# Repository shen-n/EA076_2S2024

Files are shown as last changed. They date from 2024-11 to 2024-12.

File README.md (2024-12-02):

# `ObservaCÃO - um ajudante para observação do céu noturno` ([Manual de Uso aqui](https://github.com/shen-n/EA076_2S2024/blob/main/manual_de_uso.md))

Este trabalho trata-se do projeto final da disciplina *EA076 (Laboratório de Sistemas Embarcados)*, ministrada pelo Prof. Dr. Fabiano Fruett no segundo semestre de 2024. Ele foi baseado no trabalho "[_Star Track - Arduino Powered Star Pointer and Tracker_](https://www.instructables.com/Star-Track-Arduino-Powered-Star-Pointer-and-Tracke/)", de Görkem, sendo adaptado para operar com a placa BitDogLab.

|Nome do aluno  | RA | Curso|
|--|--|--|
| Felipe Hiroshi Kano Inazumi | 215696  | Eng. Elétrica|
| Nathan Shen Baldon  | 242448 | Eng. Elétrica|

## Descrição do Projeto

O projeto buscou a construção de um sistema capaz de apontar para corpos celestes com um laser, independente da posição do observador. Para isso, deve-se fornecer ao dispositivo as coordenadas do corpo celeste que se deseja observar. Um dos requisitos foi de que o dispositivo construído fosse _wireless_, ou seja, independente de cabos para alimentação e comunicação, para que pudesse ser usado em campo com maior facilidade. 

Potenciais usuários:
- amantes de astronomia e astrofotografia;
- educadores;

## Metodologia

O desenvolvimento deste projeto envolveu quatro frentes: (a) estudo teórico sobre localização de corpos celestes (resumido no sistemas de coordenadas escolhido); (b) escolha de materiais; (c) desenvolvimento e fabricação de uma estrutura mecânica; (d) desenvolvimento e fabricação de uma PCB; (e) desenvolvimento do programa. 

### Sistemas de coordenadas

Optou-se por utilizar coordenadas do Sistema Horizontal neste projeto, ou seja, são usados os valores de Azimute e Altitude para localização de cada corpo celeste. O seguinte _site_ foi usado para determinação das coordenadas: [base de dados de corpos celestes](https://www.timeanddate.com/astronomy/night/). Mais detalhes sobre sistemas de coordenadas são fornecidos no **Apêndice A**.

### Materiais Utilizados

Os materiais escolhidos e utilizados são descritos na tabela a seguir. Se desejado, pode-se clicar no nome do material para ser redirecionado para o site de um fornecedor.

|Materiais | Qtde. | Descrição |
|--|--|--|
| [Placa BitDogLab](https://github.com/BitDogLab/BitDogLab/tree/main) | 1 | Controle do projeto. Além disso, os botões e joystick da placa também foram utilizados para controle pelo usuário. |
| [Motor de Passo 17HS4023](https://pt.aliexpress.com/item/1005007232266402.html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) | 2 | Para movimentar o laser. |
| [Driver DRV8825](https://pt.aliexpress.com/item/4000083334758.html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) | 2 | Para realizar a interface entre BitDogLab e motores. Este driver utiliza a interface STEP/DIR, que facilita o controle dos motores, sendo necessários apenas 2 pinos na BitDogLab (mais detalhes no **Apêndice B**). |
| [Bateria 3S](https://pt.aliexpress.com/item/1005003835491136.html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) | 1 | Para que o ObservaCÃO seja independente da rede elétrica. |
| [Laser](https://pt.aliexpress.com/item/1005006719063413.html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) | 1 | Para apontar para os corpos celestes. |
| [Módulo Bluetooth HC-05](https://www.eletrogate.com/modulo-bluetooth-rs232-hc-05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[MC4]_[G]_[PMax]_Categorias&utm_content=&utm_term=&gad_source=1&gclid=CjwKCAiAjKu6BhAMEiwAx4UsAqtbrS_S_TdBN0OxV5r_2TgRlhCnLvffXhJ7JxJXbR2puQFTbAGGFxoC9gUQAvD_BwE) | 1 | Para que as coordenadas dos corpos celestes fossem passadas para a BitDogLab sem necessidade de fios. |
| [Parafusos M3 10 mm](https://pt.aliexpress.com/item/1005007219475077.html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) | 4 | Para montagem de um dos motores de passo na estrutura mecânica. |
| [Conector XT30pw fêmea 90 graus](https://pt.aliexpress.com/item/1005004957495676.html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) | 1 | Para conexão da bateria na PCB criada. |
| [Cabo com conector JST 4 pinos](https://www.makerhero.com/produto/conector-jst-4-pinos-femea/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) | 4 | Para conexão entre a BitDogLab e a PCB desenvolvida. |
| [Conector JST 4 pinos macho (I2C)](https://www.makerhero.com/produto/conector-jst-4-pinos-macho/) | 3 | Utilizados na PCB criada para conexão com a BitDogLab. |
| [Conector IDC Box 14 pinos macho](https://pt.aliexpress.com/item/1005006804603387.html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) | 1 | Utilizado na PCB criada para conexão com a BitDogLab. |
| [Cabo flat com conector IDC Box 14 pinos](https://pt.aliexpress.com/item/1005003161799870.html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) | 1 | Para conexão entre a BitDogLab e a PCB desenvolvida. |

### Estrutura Mecânica

Para integrar os motores e o laser, foi desenvolvida uma estrutura mecânica, composta de quatro partes. Elas foram desenvolvidas no _software_ AutoCad Inventor e estão na pasta [3d_models](https://github.com/shen-n/EA076_2S2024/tree/main/3d_models). As peças foram fabricadas em uma impressora 3D, utilizando filamento PLA na cor branca. A montagem foi feita conforme o arquivo [assembly.stl](https://github.com/shen-n/EA076_2S2024/blob/main/3d_models/assembly.stl). O motor da base é utilizado para determinar a coordenada Azimute e, o motor superior, para a coordenada Altitude. Assim, ao longo da documentação, são muitas vezes chamados de motores de passo Azimute e Altitude. 

### Desenvolvimento da PCB

O desenvolvimento da PCB foi feito com o auxílio do software KiCad 8.0, os arquivos de fabricação, esquemático e layout estão compactados e podem ser encontrados na pasta [PCB](https://github.com/shen-n/EA076_2S2024/tree/main/PCB).

O esquemático da placa contém um conector Box IDC de 14 pinos, necessários para realizar a comunicação das GPIOs da BitDogLab com os drives DRV8825 na PCB. Além disso, a placa possui 1 conector de dois terminais para fazer a ligação do laser e do lado destes conectores estão dispostos dois conectores I2C nos quais devem ser conectados os motores de passo superior e inferior. Para mais detalhes da PCB e o esquema de ligação veja o capítulo [Descrição Estrutural](#Descrição-Estrutural)

O circuito para acionamento do Laser foi desenvolvido com um chaveamento simples controlado por transistor conforme apresentado na figura abaixo. Para controlar o chaveamento deste transistor é necessário fazer a conexão do IDC0 no conector J7 da placa.

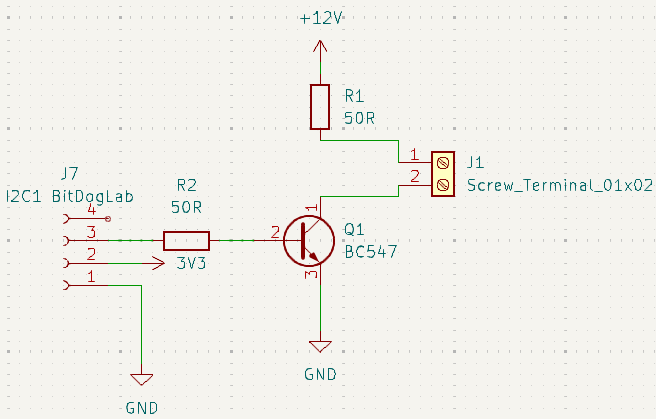
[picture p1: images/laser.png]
Laser


Além disso, a placa também conta com um header J9 de 6 pinos que permite acesso aos GPIOS 08 e 09 além do VCC e GND. 

A alimentação da placa deve ser conectada com uma bateria 3S (11.1 V) via conector XT30. Contudo, a placa também pode ser alimentada com uma tensão de até 12V, que seria a tensão nominal do motor de passo escolhido no projeto.

### Desenvolvimento do programa 

O programa utilizado neste projeto foi desenvolvido na linguagem de programação micropython e utiliza as seguintes bibliotecas:
- Machine
- Time
- Sys
- Ssd1306
- Framebuf
  
A comunicação com o módulo bluethooh foi feita via protocolo UART, e mais especificamente foi utilizada a UART0 da Raspiberry neste projeto. 

O programa inicia com uma função de calibração controlada via Joystick da BitDogLab, de tal forma que, o usuário deverá utilizar movimentos do joystick para cima/baixo ou para a esquerda/direita para controlar os motores superiores e inferiores de tal forma a alinhar o laser na posição horizontal e na direção do polo norte.

Cada comando direcional do Joystick envia o comando de 1 passo para o respectivo motor (superior ou inferior). Quando o usuário pressiona o botão central do Joystick, um delay é adicionado entre cada comando de 1 passo para o motor, resultando em um movimento mais sensível e permitindo assim uma calibração fina dos motores. Esse pressionar do botão do Joystick alterna entre os modos de calibração fina e mais rápida. Para confirmar a calibração estabelecida, o usuário deve pressionar o botão B para avançar para a próxima etapa do programa. Neste momento, o programa entende que a posição atual dos motores é a referência (0,0).

Em seguida, o programa aguarda o envio das coordenadas, via módulo bluetooth, do astro a ser apontado. As coordenadas devem ser enviadas no formato:

````
Azimuth,Altitude 
````

Note que estas coordenadas podem ser do tipo float com precisão de 2 casas decimais, e não deve haver espaço entre a virgula. Ambos as coordenadas podem ser valores negativos e caso o valor azimutal seja maior que 180°, o programa converte este valor de ângulo positivo para o respectivo ângulo negativo para evitar que o motor inferior rotacione mais do que o necessário.

Por fim, o programa calcula o número de micropassos necessários para cada motor de tal forma que, o motor finalize o movimento no ângulo enviado pelo usuário.

Alguns exemplos de comandos enviados na sequência:

Enviando 45,45
````
45,45
````
O motor inferior irá girar 45° para Leste e o motor superior irá rotacionar 45° para cima, resultando em Azimuth: 45°, Altitude: 45°

Enviando 90,90
````
90,90
````
O motor inferior irá girar 45° novamente para Leste e o motor superior irá rotacionar novamente 45° para cima, resultando em Azimuth: 90°, Altitude: 90°

Enviando 0,0
````
0,0
````
O motor inferior irá girar -90° para Leste (equivalente à 90° para oeste) e o motor superior irá rotacionar -90° para cima (equivalente à 90° para baixo), resultando em Azimuth: 0°, Altitude: 0° (origem)

Enviando 270,0
````
270,0
````
O motor inferior irá girar 270° para Leste (equivalente à 360-270 = 90° para oeste) e o motor superior irá rotacionar 0° para cima resultando em Azimuth: -90°, Altitude: 0° 

Entre cada envio das coordenadas, o usuário também pode pressionar o Botão A ou Botão B da BitDogLab e uma das situações a seguir deve ocorrer:
- Botão A: Alterna o estado do Laser para Ligado/Desligado
- Botão B: O programa entra no modo de calibração, conforme mencionado anteriormente, sendo necessário pressionar novamente o botão B para concluir a calibração. 

Abaixo é apresentado um fluxograma do programa descrito

- **Fluxograma:**



## Descrição Estrutural

Para que se compreenda a conexão entre os diferentes componentes, foi criada a tabela abaixo, que apresenta qual GPIO da BitDogLab foi atribuída a cada pino de cada periférico. Além disso, na coluna mais à direita, é apresentado em qual conector cada GPIO se situa.

Obs: note que os pinos de ajuste de micropasso dos dois _drivers_ (M0, M1 e M2) estão conectados entre si, não sendo possível configurá-los de forma independente.

### Conexões com BitDogLab
<table><thead><tr><th></th><th>Pino</th><th>GPIO</th><th>Conector BitDogLab</th></tr></thead><tbody><tr><td rowspan="5">Driver 1 (motor Altitude)</td><td>M0</td><td>19</td><td rowspan="10">IDC box 14 pinos</td></tr><tr><td>M1</td><td>20</td></tr><tr><td>M2</td><td>18</td></tr><tr><td>DIR</td><td>4</td></tr><tr><td>STEP</td><td>28</td></tr><tr><td rowspan="5">Driver 2 (motor Azimute)</td><td>M0</td><td>19</td></tr><tr><td>M1</td><td>20</td></tr><tr><td>M2</td><td>18</td></tr><tr><td>DIR</td><td>17</td></tr><tr><td>STEP</td><td>16</td></tr><tr><td>Laser</td><td>-</td><td>2 (SDL)</td><td>I2C1</td></tr><tr><td rowspan="4">Módulo Bluetooth HC-05</td><td>RX</td><td>0 (SDA)</td><td rowspan="4">I2C0</td></tr><tr><td>TX</td><td>1 (SCL)</td></tr><tr><td>VCC</td><td>3V3</td></tr><tr><td>GND</td><td>GND</td></tr></tbody></table>

Também, para facilitar a montagem, a figura abaixo mostra quais conexões devem ser feitas entre a BitDogLab e todos os periféricos.

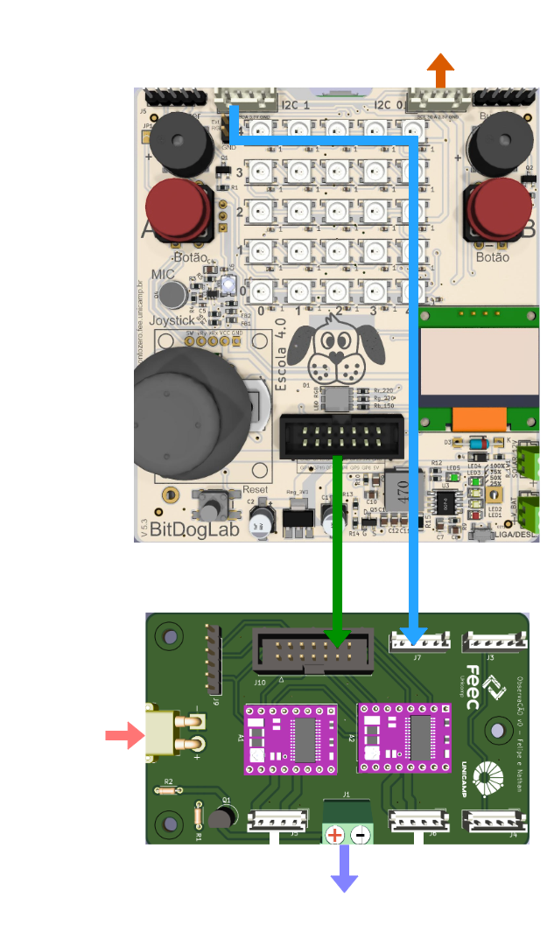
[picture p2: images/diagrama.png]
diagrama


## Resultados

A figura abaixo apresenta o resultado da montagem da estrutura mecânica. Como pode se constatar, ficou exatamente conforme o modelo 3D projetado.

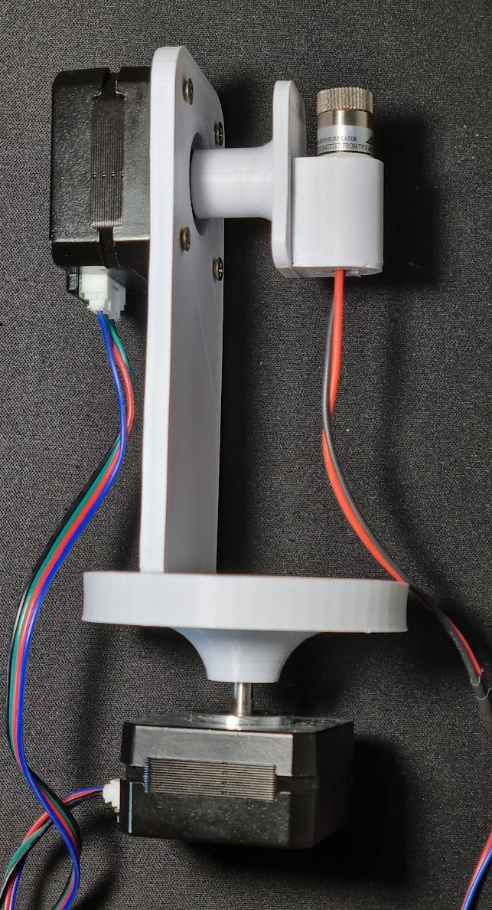
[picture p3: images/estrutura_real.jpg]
estrutura_real


A montagem da PCB também foi um sucesso, sendo apresentada abaixo.

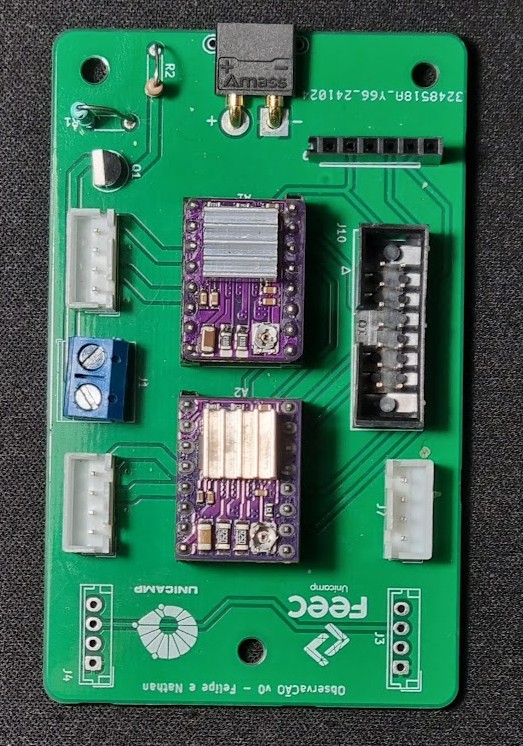
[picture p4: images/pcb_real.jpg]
pcb_real


Em relação ao funcionamento do dispositivo para observação do céu, não foi possível visualizar o _laser_ durante a noite (muito fraco), sendo que não foi possível analisar sua precisão. No entanto, foram utilizados aplicativos de celular que localizam corpos celestes (e.g. [Star Walk 2](https://play.google.com/store/apps/details?id=com.vitotechnology.StarWalk2Free&hl=pt_BR)) e, em testes, o sistema ObservaCÃO apontou aproximadamente para a mesma direção indicada pelos aplicativos, mostrando potencial. No entanto, havia sempre algum erro entre o celular e o dispositivo, principalmente pela calibração falha em **ambos** os dispositivos, o que será discutido na próxima seção.  

## Desafios e Conclusão

Ao longo do desenvolvimento do projeto, houve apenas desafios pequenos. Primeiramente, pode-se citar o mau funcionamento das GPIOs 8 e 9 (UART1), que seriam usadas com o módulo bluetooth HC-05. Em nenhum momento, foi possível ler ou escrever dados com estes pinos, mesmo realizando a atribuição explícita deles para UART1 no programa. Assim, foi necessário utilizar a UART0 (GPIOs 0 e 1), a qual funcionou. No tempo do projeto, não foi possível identificar o problema com a UART1. Vale comentar também que o módulo bluetooth apresentou inconsistências, ora lendo e escrevendo corretamente, ora não.

Outro problema encontrado ao longo do desenvolvimento do projeto foram falhas em fios/cabos: um deles foi um _jumper_ de _protoboard_, o qual estava rompido internamente; outro foi com a crimpagem do cabo flat utilizado, que apresentou falhas de continuidade e precisou ser ajustado.

Por fim, o desafio mais relevante foi aquele relacionado com erros na indicação de corpos celestes. Uma das grandes fontes de erro foi a calibração do celular, que estava sendo usado como referência de bússola e como referência da localização dos corpos celestes. Note que, neste caso, qualquer erro nesta referência causa erros no dispositivo ObservaCÃO e a própria indicação dos astros dada pelo celular pode estar também equivocada. Para corrigir isso, poderia ter sido utilizado o Sistema Equatorial (descrito no **Apêndice A**) e alguma estrela conhecida como referência, o que eliminaria, ao menos, uma fonte de erro. A dificuldade de se usar este sistema, entretanto, foi de que toda a estrutura mecânica teria de ser alinhada com o plano fundamental desse sistema, o que não foi possível neste projeto, mas que poderia ser considerado em uma próxima versão do dispositivo.

Assim, encerra-se indicando possíveis melhorias futuras: (a) melhorar estabilidade da estrutura mecânica, a qual atualmente tomba durante movimentos bruscos dos motores; (b) adicionar peça para acoplamento do dispositivo ObservaCÃO com tripé, o que permitiria incliná-lo e alinhá-lo com o plano fundamental do Sistema Equatorial; (c) adicionar conexão entre pinos ENABLE dos drivers e BitDogLab, para que seja possível ativar e desativar os motores quando desejado, o que aumentaria a autonomia da bateria.

## Referências

[1] GörkemPortfolio, “Star Track - Arduino Powered Star Pointer and Tracker,” Instructables. https://www.instructables.com/Star-Track-Arduino-Powered-Star-Pointer-and-Tracke/

[2] “Coordinate Systems Comparison,” Unl.edu, 2024. https://astro.unl.edu/classaction/animations/coordsmotion/celhorcomp.html.

[3] “Galileo’s Finger - an Open Source Astronomy Learning Tool,” Instructables, Mar. 30, 2015. https://www.instructables.com/Galileos-Finger-An-Open-Source-Astronomy-Learning-/.

[4] P. Dyches, “What is the North Star and How Do You Find It? - NASA Science,” science.nasa.gov, Jul. 28, 2021. https://science.nasa.gov/solar-system/skywatching/what-is-the-north-star-and-how-do-you-find-it/

[5] “The North Star: Polaris,” Space.com, May 16, 2017. https://www.space.com/15567-north-star-polaris.html

[6] “Horizontal and equatorial coordinate systems,” Astronomy Stack Exchange, Dec. 31, 2021. https://astronomy.stackexchange.com/questions/48004/horizontal-.

[7] “Sistema horizontal de coordenadas,” Wikipedia.org, Jul. 2007. https://pt.wikipedia.org/wiki/Sistema_horizontal_de_coordenadas.

[8] “The Internet Stellar Database,”. http://www.stellar-database.com/

## Apêndice A - sistemas de coordenadas

Para localizar corpos celestes, é muito comum que se utilize o sistema de coordenadas celeste. Nele, usa-se o conceito de Esfera Celeste: uma projeção de todo o céu em uma esfera de raio indeterminado e concêntrica à Terra (como se o céu que vemos fosse uma casca esférica ao redor da Terra). A localização dos corpos se dá através de coordenadas esféricas, as quais dependem do plano fundamental escolhido (plano que divide Esfera Celeste em dois hemisférios) [1]. O Sistema Horizontal, por exemplo, é geralmente mais conhecido (com Azimute/Altitude como coordenadas) e utiliza o horizonte local do observador como plano fundamental [1,7]. O problema é que, como a referência (plano fundamental) depende da posição do observador na Terra, a posição do corpo celeste a ser apontado, por consequência, também depende. Assim, para eliminar essa dependência, é comum que se utilize o Sistema Equatorial, que toma como plano fundamental o Equador Celeste (projeção da Linha do Equador na Esfera Celeste) [1,6]. O Polo Norte e Polo Sul também são projetados na Esfera Celeste, sendo denominados Polo Sul Celeste e Polo Norte Celeste.

As coordenadas são dadas em Ascenção Reta e Declinação:
- Declinação (DEC): ângulo entre Equador Celeste e Polos Norte ou Sul Celestes (varia de -90 a 90°).
- Ascensão Reta (RA): ângulo ao longo do Equador Celeste em relação a uma referência zero (ponto vernal - equivalente ao Meridiano de Greenwich como referência de longitude). Ele é dado em horas, minutos e segundos, de forma que uma volta completa equivale a 24h.

Assim, para localizar os corpos celestes, pode-se utilizar uma base de dados que indique as coordenadas no Sistema Equatorial [1,8]. Também, o sistema precisa saber onde estão as referências de posição necessárias:
- Referência para DEC: uma alternativa é encontrar o Polo Norte Celeste, que pode ser encontrado através da Estrela Polar (Polaris) [1,4,5]. Assim, seria necessário apontar para esta Estrela manualmente, indicando para o sistema sua posição (obs: esta estrela é visível apenas no hemisfério Norte, sendo necessário outra referência para observadores do hemisfério Sul).
- Referência para RA: pode-se utilizar o tempo sideral, que também tem como referência o ponto vernal (referência de RA). O tempo sideral pode ser calculado a partir do horário local. [1]

## Apêndice B - driver DRV8825

O driver DRV8825 possui duas pontes H e é projetado para controle de motores de passo bipolares. O controle é feito com a interface STEP/DIR, entradas que indicam quantos passos devem ser dados (definido pelo número de pulsos em STEP) e em qual direção (definido pelo nível lógico em DIR) (figura abaixo). 

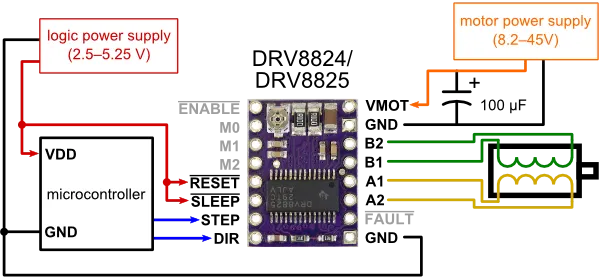
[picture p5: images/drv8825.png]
drv8825

Retirado de: [fonte](https://www.marinostore.com/automacao/driver-motor-de-passo-drv8825)

Para controle do tamanho do passo (microstep), é necessário introduzir uma combinação de valores binários nas entradas M0, M1 e M2, conforme apresentado na tabela abaixo. O driver possui uma resistência de pulldown interna, de tal forma que, se a entrada estiver desconectada o nível de tensão neste terminal está em 0V (GND).

<table><thead><tr><th>M2</th><th>M1</th><th>M0</th><th>Tamanho do Passo</th></tr></thead><tbody><tr><td>0</td><td>0</td><td>0</td><td>Passo completo</td></tr><tr><td>0</td><td>0</td><td>1</td><td>1/2 Passo</td></tr><tr><td>0</td><td>1</td><td>0</td><td>1/4 Passo</td></tr><tr><td>0</td><td>1</td><td>1</td><td>1/8 Passo</td></tr><tr><td>1</td><td>0</td><td>0</td><td>1/16 Passo</td></tr><tr><td>1</td><td>0</td><td>1</td><td rowspan="3"><br><br>1/32 Passo</td></tr><tr><td>1</td><td>1</td><td>0</td></tr><tr><td>1</td><td>1</td><td>1</td></tr></tbody></table>

Outra etapa necessária para o funcionamento do driver DRV8825 é a calibração da corrente de saída do driver. Esta calibração é feita alterando a posição do potenciômetro disponível no próprio driver, e fazendo a medição do valor de tensão entre este ponto e o GND. 

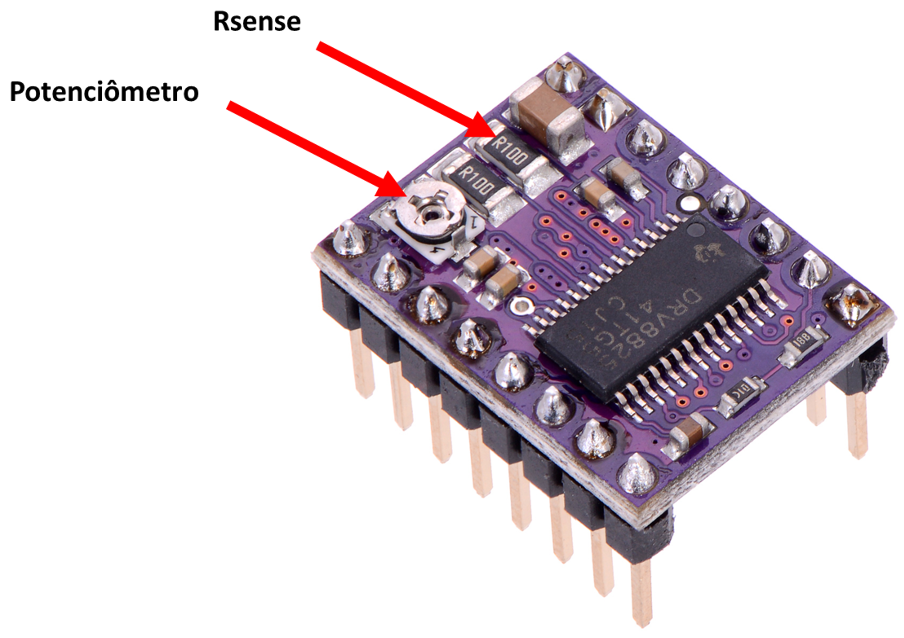
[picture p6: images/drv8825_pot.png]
drv8825_pot


Com este valor de tensão, a corrente de saída do driver é calculada pela seguinte equação:

$$I_{OUT}= \dfrac{V_{Ref}}{Av \cdot R_{sense}}$$

Onde Vref é o valor da tensão medida no potênciometro, Av = 5 para este driver e o Rsense pode ser encontrado no driver conforme apresentado na figura acima.

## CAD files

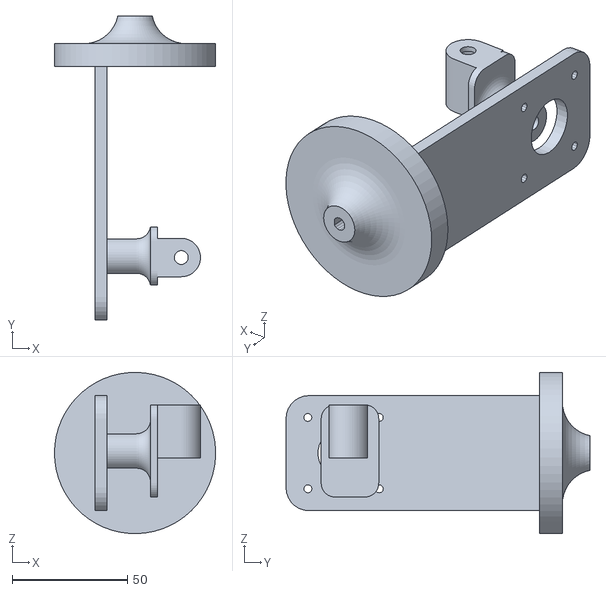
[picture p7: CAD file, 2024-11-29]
3d_models/assembly.stl
70.0 x 132.0 x 70.0

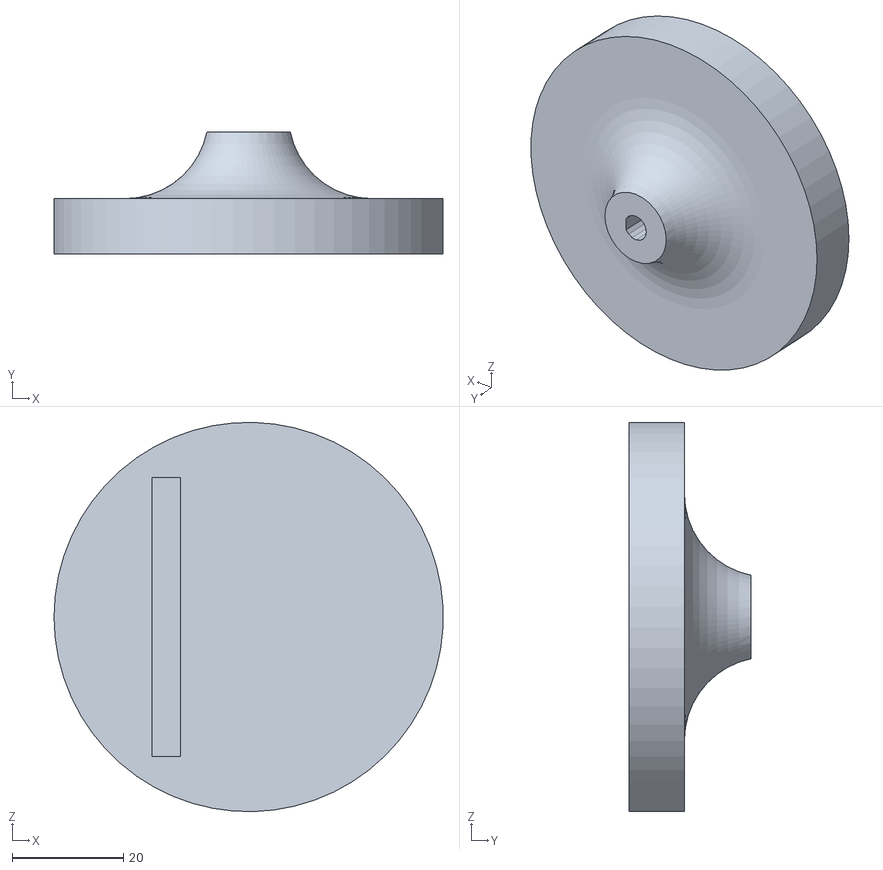
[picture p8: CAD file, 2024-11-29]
3d_models/plate.stl
70.0 x 22.0 x 70.0

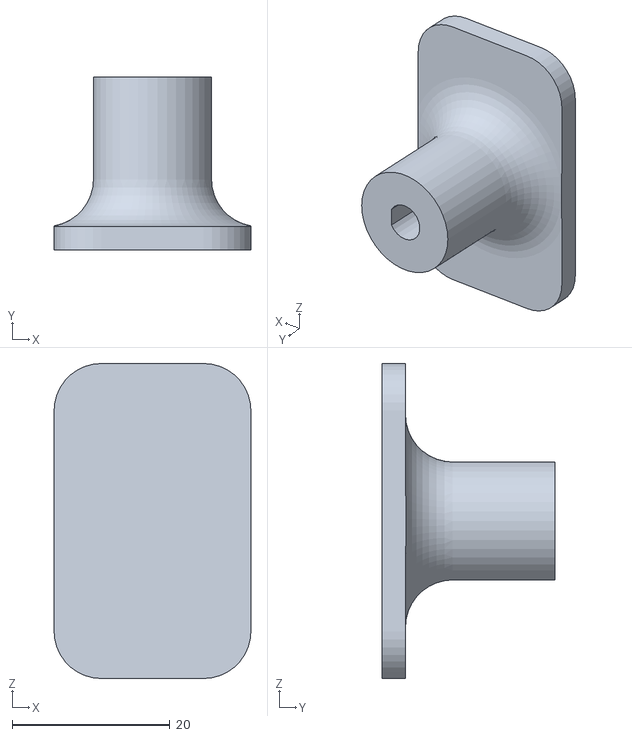
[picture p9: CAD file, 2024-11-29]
3d_models/encaixe_giro.stl
25.0 x 22.0 x 40.0

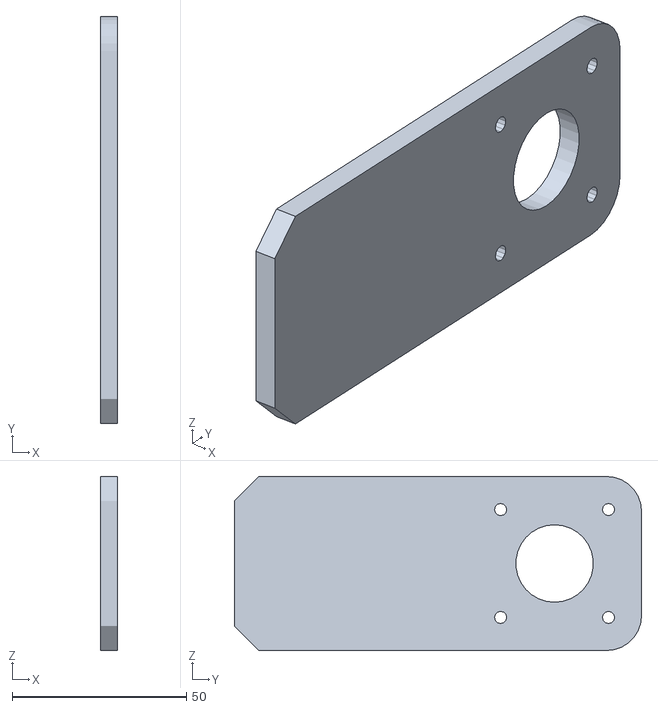
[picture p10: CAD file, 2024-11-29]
3d_models/suporte_vertical.stl
5.00 x 117.0 x 50.0

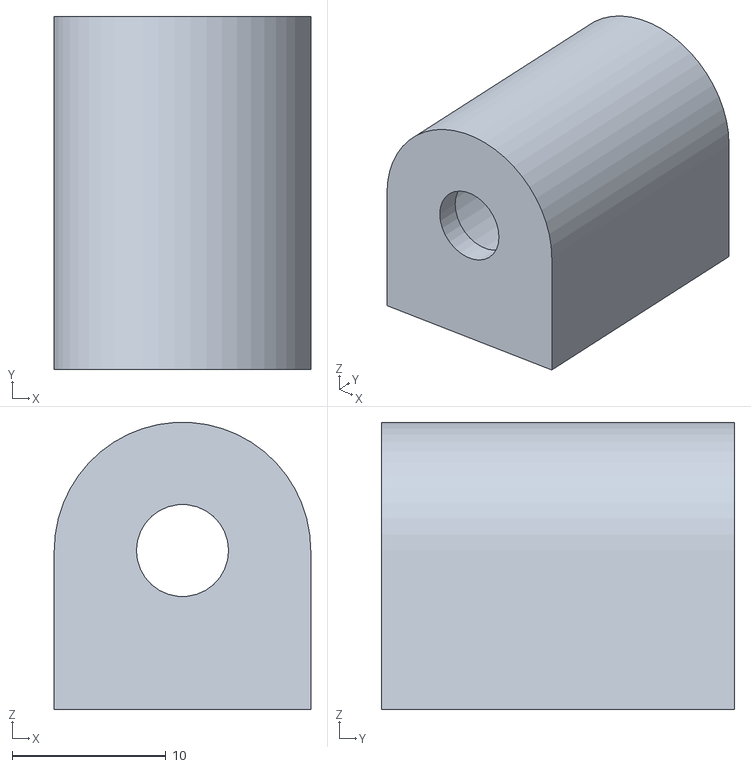
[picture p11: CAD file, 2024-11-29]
3d_models/suporte_laser_v2.stl
16.7 x 23.0 x 18.7

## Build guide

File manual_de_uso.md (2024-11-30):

# `Manual de Uso - ObservaCÃO`

Tenha em mãos: observaCÃO (BitDogLab, PCB ObservaCÃO e estrutura mecânica com laser e motores), bússola, celular com bluetooth, acesso à base de dados de corpos celestes (pode ser acessado pelo celular).

| Etapa  | Ação |
|--|--|
| 1  | Carregar programa na placa BitDogLab |
| 2  | Realizar montagem do ObservaCÃO conforme figura abaixo. |
| 3 | Instalar e abrir app ["Serial Bluetooth Terminal_"](https://play.google.com/store/apps/details?id=de.kai_morich.serial_bluetooth_terminal&hl=pt_BR) | 
| 4 |  Parear e conectar celular com módulo HC-05 (senha: 1234)|
| 5 | Alinhar _laser_ com a linha do horizonte |
| 6 | Com auxílio de uma bússola, apontar _laser_ para o sentido Norte |
| 7 | Abrir [base de dados de corpos celestes](https://www.timeanddate.com/astronomy/night/) |
| 8 |  Procurar nome do corpo celeste que se deseja observar e copiar coordenadas (Azimute e Altitude) |
| 9 |  Inserir no terminal _bluetooth_ as coordenadas, no formato: Azimute,Altitude |
| 10 |  Pronto! |

Montagem ObservaCAO

Existem ainda outras duas funcionalidades: calibração e segurança.

## Calibração

Esse modo pode ser utilizado para recalibrar o dispositivo caso apresente erros ou caso seja movimentado. 

| Etapa  | Ação |
|--|--|
| 1  | Pressionar **botão B** para ativar modo de calibração |
| 2  | Mover o _joystick_ para redirecionar aproximadamente o sentido do _laser_ para o Norte|
| 3 | Pressionar _joystick_ para ativar ajuste fino. | 
| 4 | Mover o _joystick_ (velocidade mais lenta) garantindo o melhor alinhamento possível com o norte |
| 5 | Pressionar novamente **botão B** para finalizar calibração. |

## Segurança

Para proteção ocular e evitar que o _laser_ atinja aeronaves, o **botão A** pode ser pressionado para que o _laser_ fique desativado enquanto é movimentado.

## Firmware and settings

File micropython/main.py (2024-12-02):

# Libraries
from machine import Pin
from time import sleep_ms, sleep
import sys
from machine import Pin, ADC, SoftI2C, PWM
from ssd1306 import SSD1306_I2C
import framebuf
import neopixel
import time
import random
from machine import Pin, UART


############## INIT/CONFIG PORTS
        
 # Configura UART0
uart = UART(0, 9600)

# Inicializa o joystick
adc_x = ADC(Pin(27))
adc_y = ADC(Pin(26))
joystick_button = Pin(22, Pin.IN, Pin.PULL_UP)

# Define os valores mínimos e máximos dos conversores AD
adc_min = 300
adc_max = 65535
adc_avg = int((adc_max-adc_min)/2)
tol = 30000 # tolerance to arbitrate between right/left movement

# Inicialização de variáveis para controle do display OLED.
i2c = SoftI2C(scl=Pin(15), sda=Pin(14))
oled = SSD1306_I2C(128, 64, i2c)
oled.fill(0)

# Configura pinos de microstep do motor
m0Pin = Pin(19, Pin.OUT)
m1Pin = Pin(20, Pin.OUT)
m2Pin = Pin(18, Pin.OUT)

# create an output pin on pin #0
dirPin_zen = Pin(4, Pin.OUT) #laser
stepPin_zen = Pin(28, Pin.OUT) #laser
dirPin_azi = Pin(17, Pin.OUT) #base
stepPin_azi = Pin(16, Pin.OUT) #base

laserPin = Pin(2, Pin.OUT) # laser

laserPin.value(1)

botao_b = Pin(6, Pin.IN, Pin.PULL_UP)
button_a = Pin(5, Pin.IN, Pin.PULL_UP)


############## FUNCTIONS

# takes a step (Azimuth)
def step_x():
    stepPin_azi.value(1)
    sleep_ms(3)
    stepPin_azi.value(0)
    sleep_ms(3)
    
# takes a step (Zenith)
def step_y():
    stepPin_zen.value(1)
    sleep_ms(3)
    stepPin_zen.value(0)
    sleep_ms(3)

# indicates if joystick is being pushed up or down
def up_or_down(adc_value, adc_avg):
    if (adc_value<(adc_avg-tol)):
        return 'up'
    if adc_value>(adc_avg+tol):
        return 'down'
    else:
        return None

# indicates if joystick is being pushed to the left or to the right
def left_or_right(adc_value, adc_avg):
    if (adc_value<(adc_avg-tol)):
        return 'left'
    if adc_value>(adc_avg+tol):
        return 'right'
    else:
        return None
    
# converts angle (degrees) to step (1/32 microstepping)
# 1 step = 1.8 degrees
def degrees2step(angle):
    microstep = 1.8/32 # degrees
    n_steps = int(angle/microstep)
    return n_steps

# sets new reference for Zenith and Azimuth angles
def set_reference():
    azi_angle = 0
    zen_angle = 0

# recalibrates both step motors using BitDogLab joystick
def recalibrate(dirPin_x, dirPin_y, adc_x, adc_y, joystick_button, botao_b, oled):
    previous_pos_x = None
    previous_pos_y = None
    joystick_button_pressed = False
    micro_adjust = False
    
    oled.fill(0)
    oled.text("CALIBRACAO", 20, 15)
    oled.show()
    
    button_b_pressed = False

    # Waits user calibration
    while True:
        adc_value_x = adc_x.read_u16()
        adc_value_y = adc_y.read_u16()
   
        # Reads Joystick postion
        current_pos_x = left_or_right(adc_value_x, adc_avg)
        current_pos_y = up_or_down(adc_value_y, adc_avg)
        
        # Reads Joystick button status
        joystick_button_state = joystick_button.value()
        
        
        # Verify if joystick was pressed and released
        if joystick_button_state == 0 and not joystick_button_pressed:
            joystick_button_pressed = True
            micro_adjust = not micro_adjust
        
    
        if joystick_button_state == 1:
            joystick_button_pressed = False
        
        
        # If Joystick to the right, then moves the motor
        if current_pos_x == 'right':                  
            if previous_pos_x != 'right':
                oled.text("DIREITA", 30, 50)
                oled.show()
                dirPin_x.value(0)
                previous_pos_x = 'right'

            
            step_x()
            if micro_adjust:
                sleep_ms(50)
            
            
        # If Joystick to the left, then moves the motor
        elif current_pos_x == 'left':            
            if previous_pos_x != 'left':
                oled.text("ESQUERDA", 30, 50)
                oled.show()
                dirPin_x.value(0)
                dirPin_x.value(1)
                previous_pos_x = 'left'

            
            step_x()
            if micro_adjust:
                sleep_ms(50)
        
        
        # Else, do nothing
        elif current_pos_x == None:
            if previous_pos_x != None:
                previous_pos_x = None
                oled.fill(0)
                oled.text("CALIBRACAO", 20, 15)
                oled.show()

        
        # If Joystick is up, then moves the motor
        if current_pos_y == 'up':                  
            if previous_pos_y != 'up':
                oled.text("CIMA", 30, 50)
                oled.show()
                dirPin_y.value(0)
                previous_pos_y = 'up'

            
            
            if micro_adjust:
                sleep_ms(50)
            step_y()
        
        # If Joystick is down, then moves the motor
        elif current_pos_y == 'down':            
            if previous_pos_y != 'down':
                oled.text("BAIXO", 30, 50)
                oled.show()
                dirPin_y.value(1)
                previous_pos_y = 'down'

            
            
            if micro_adjust:
                sleep_ms(50)
            step_y()
        
        
        # Else, do nothing
        elif current_pos_y == None:
            if previous_pos_y != None:
                oled.fill(0)
                oled.text("CALIBRACAO", 20, 15)
                oled.show()
                previous_pos_y = None
        
        # Checks is button b was pressed 
        if botao_b.value()==0:
            button_b_pressed = True
        
        # Checks is button b was pressed and released then left function
        elif button_b_pressed and botao_b.value():
            return 0,0
 
            


############## MAIN

# configures microstep pins (to 1/32)
m0Pin.value(1)
m1Pin.value(1)
m2Pin.value(1)

# sets initial reference (for Zenith and Azimuth angles):
zen_angle = 0
azi_angle = 0


zen_angle, azi_angle = recalibrate(dirPin_azi, dirPin_zen, adc_x, adc_y, joystick_button, botao_b, oled)

oled.fill(0)
oled.text("ENVIE COORDENADAS", 0,15)
oled.text("NO FORMATO", 25,25)
oled.text("Azimuth,Altitude", 0,45)
oled.show()

led_state = 0
laserPin.value(1)

while True:
    
    ############## Zenith
    
    uart.write('Zenith Angle (0 a 90): \n')
    
    # flags
    wait = True
    button_b_pressed = False
    button_a_pressed = False
    
    # Samples data, Button A, Button B from BitDogLab
    while wait:
        # Checks if button B was pressed
        if botao_b.value() == 0:
            button_b_pressed = True
        
        # Checks if button B was already pressed and released
        elif botao_b.value() == 1 and button_b_pressed:
            button_b_pressed = False
            
            # enters calibration mode
            zen_angle, azi_angle = recalibrate(dirPin_azi, dirPin_zen, adc_x, adc_y, joystick_button, botao_b, oled)
           
            oled.fill(0)
            oled.text("ENVIE COORDENADAS", 0,15)
            oled.text("NO FORMATO", 25,25)
            oled.text("Azimuth,Altitude", 0,45)
            oled.show()
        
        # Checks if button A was pressed
        if button_a.value() == 0:
            button_a_pressed = True
        
        # Checks if button A was already pressed and released
        elif button_a.value() == 1 and button_a_pressed:
            # Led Off
            if led_state == 0:
                led_state = 2
                laserPin.value(0)
            
            # Led On
            elif led_state == 2:
                led_state = 0
                laserPin.value(1)
            button_a_pressed = False
        
        # Verify if data is avaliable
        if uart.any():  
            data = uart.read().decode('utf-8').strip()  # Read and remove white spaces
            try:
                # Splits data received by comma
                values = data.split(',')
                if len(values) == 2:  # certify if threre is only two values
                    azi_input = float(values[0])  # Converts azimuth to float
                    zen_input = float(values[1])  # Converts alitude to float
                    wait = False
                    print(f"Zenith: {zen_input}, Azimuth: {azi_input}")
            except ValueError:
                print("Dados recebidos inválidos. Certifique-se de enviar no formato 20,20.")
    
    # Verify if azimuth is greater than 180, and if so, changes its value to
    # the corresponding negative angle value
    if azi_input > 180:
        azi_input = (-1)*(360 - azi_input)

    if led_state == 1:
        laserPin.value(0)
                        
    # calculates the needed rotation to reach the input angle
    zen = zen_input - zen_angle
    
    # determines direction of rotation 
    if zen<0:
        dirPin_zen.value(1)
        zen = -zen # turns into positive number
    else:
        dirPin_zen.value(0)
        
    # converts calculated angle in degrees to number of microsteps (1/32) needed
    zen_steps = degrees2step(zen)
    
    ############## Azimuth
        

    uart.write('Zenith Angle: {} deg. \n'.format(zen_input))
    uart.write('Azimuth Angle: {} deg. \n'.format(azi_input))

    # calculates the needed rotation to reach the input angle
    azi = azi_input-azi_angle
    
    # determines direction of rotation 
    if azi<0:
        dirPin_azi.value(1)
        azi = -azi # turns into positive number
    else:
        dirPin_azi.value(0)
    
    # converts calculated angle in degrees to number of microsteps (1/32) needed
    azi_steps = degrees2step(azi)
    
    # displays configured angles in the OLED
    oled.fill(0)

    oled.text("-"*30,0,0)
    oled.text(f"AZIMUTH: {azi_input:.2f}", 5, 10)
    oled.text(f"ALTITUDE: {zen_input:.2f}", 5, 25)

    oled.text("-"*30,0,35)
        
        
    oled.text("A: LASER", 5, 45)
    oled.text("B: CALIBRACAO", 5, 55)

    oled.show()
    
    # moves to new position
    for i in range(azi_steps):
        step_x()
    for i in range (zen_steps):
        step_y()
        
    # update current position (in relation to the reference set earlier)
    zen_angle = zen_input
    azi_angle = azi_input
    
    if led_state == 1:
        laserPin.value(1)

    
